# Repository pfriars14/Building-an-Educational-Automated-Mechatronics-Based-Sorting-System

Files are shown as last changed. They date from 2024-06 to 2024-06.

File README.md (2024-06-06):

The project integrates mechanical and electrical design, incorporating a robot arm, a microcontroller, sensors, and actuators. The sorting machine uses color identification to sort wooden blocks of three different colors. The blocks are stacked and dropped onto a conveyor belt by a hopper system that employs a solenoid actuator and a servo to release one block at a time at specific intervals. As the belt runs continuously, each block passes under a color sensor, which monitors the color and signals one of three servo-powered mechanical arms to guide the block into the appropriate chute. Each chute is equipped with a capacitive proximity sensor that sends a voltage signal to the robot controller, queuing commands for the robot to pick up the blocks from the bottom of each chute and return them to the hopper to form a continuously running sorting system. The project exemplifies a low-cost system that can be used in mechatronics education to illustrate the many challenges encountered in developing automated sorting systems.

This github site details project CAD files, videos, Arduino code, and a bill of materials.

NOTE: For the CAD section, "Ben Updated Design" is the final assembly, the rest of the files are parts which just need to be in the path in order to load. There is also another folder which just as a .step and .sldprt file for viewing the assembly surface geomtry.

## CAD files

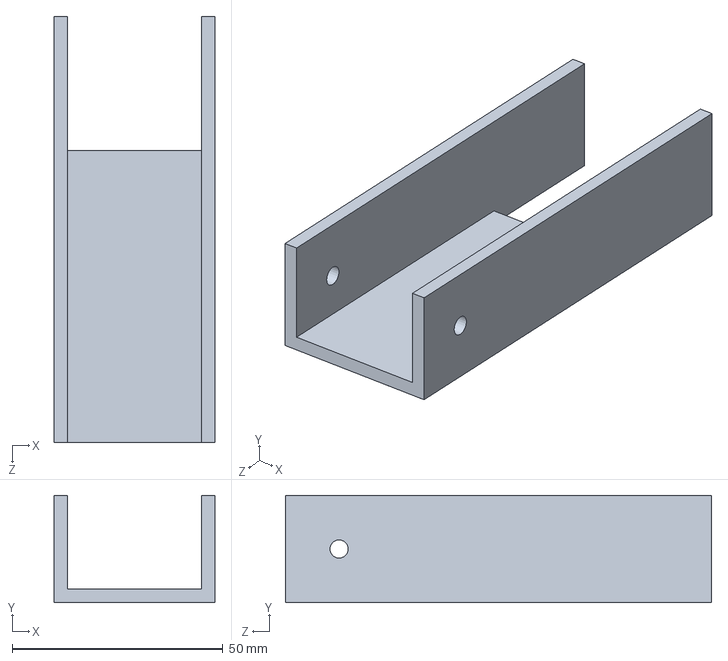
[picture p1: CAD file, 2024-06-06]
CAD Models/Wide Channel for Dropper.SLDPRT
38.1 x 25.4 x 101.0 mm

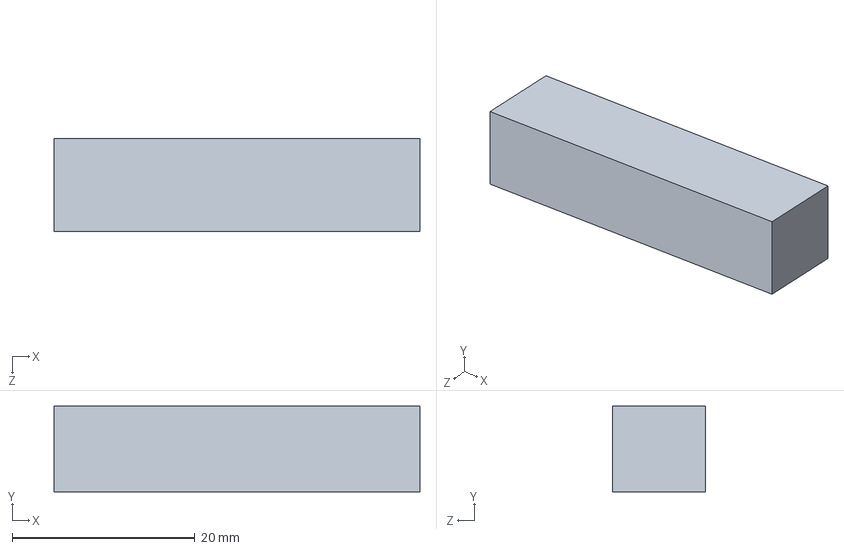
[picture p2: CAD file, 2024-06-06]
CAD Models/Body2.SLDPRT
40.0 x 9.36 x 10.2 mm

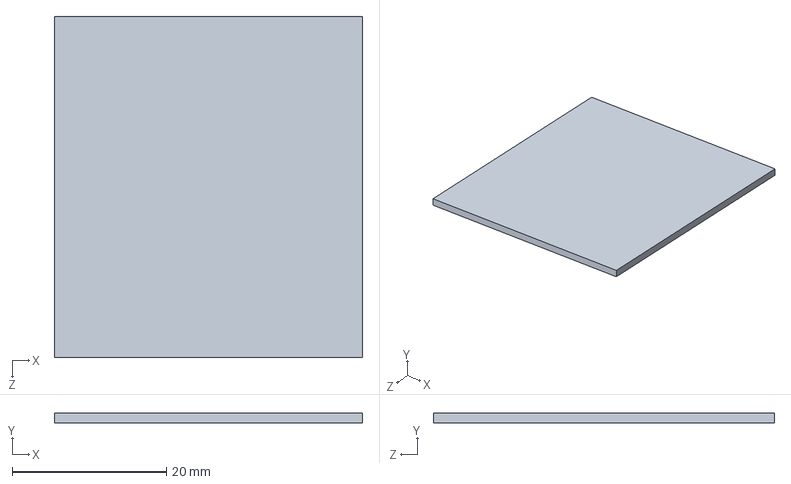
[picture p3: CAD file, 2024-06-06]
CAD Models/Body1.SLDPRT
40.0 x 1.27 x 44.3 mm

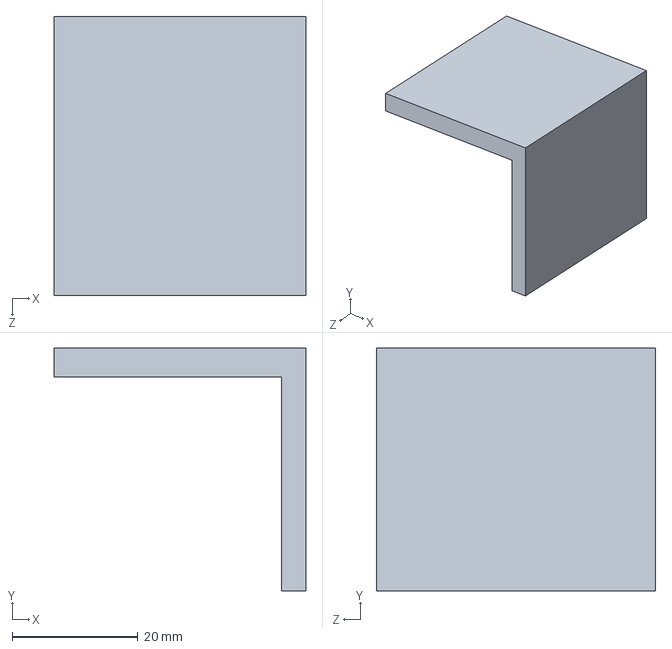
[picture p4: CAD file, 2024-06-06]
CAD Models/Body4.SLDPRT
40.0 x 38.6 x 44.3 mm

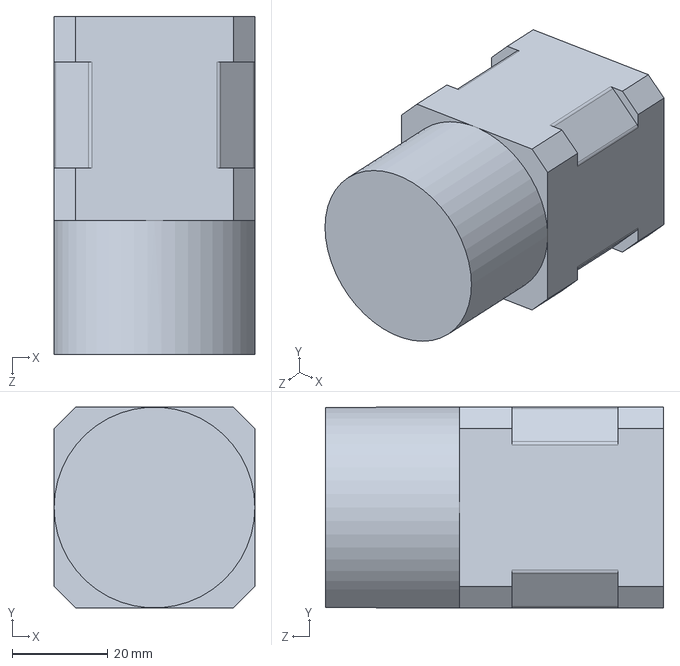
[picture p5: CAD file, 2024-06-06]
CAD Models/Stepper Motor.SLDPRT
42.0 x 42.0 x 70.7 mm

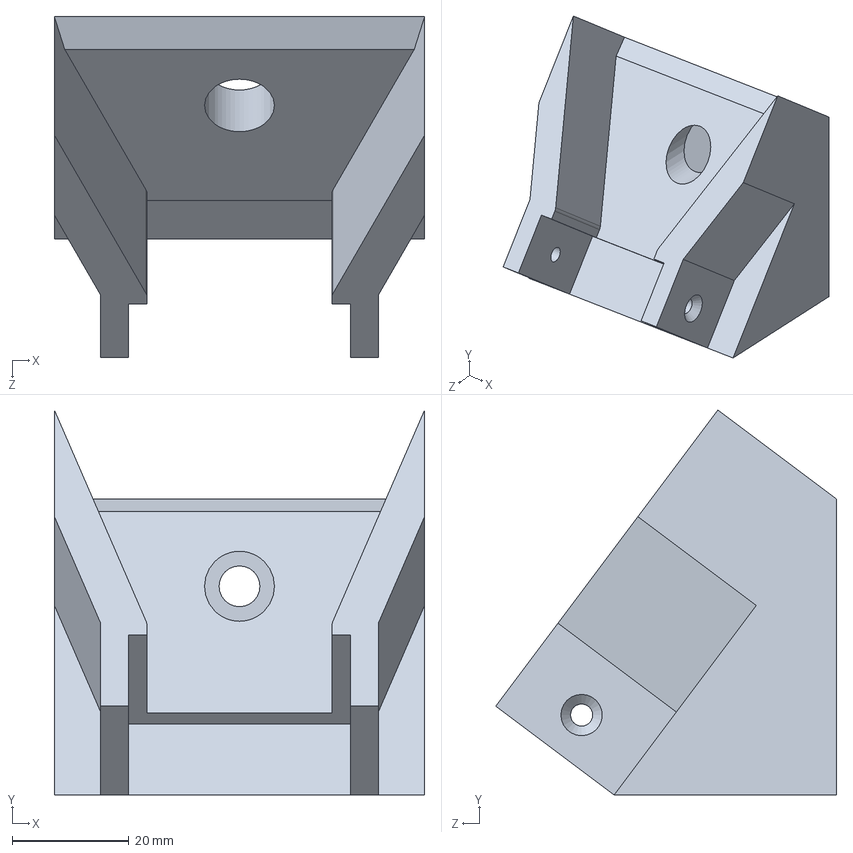
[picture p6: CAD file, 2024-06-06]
CAD Models/Ramp Attachment.SLDPRT
63.5 x 66.0 x 58.4 mm

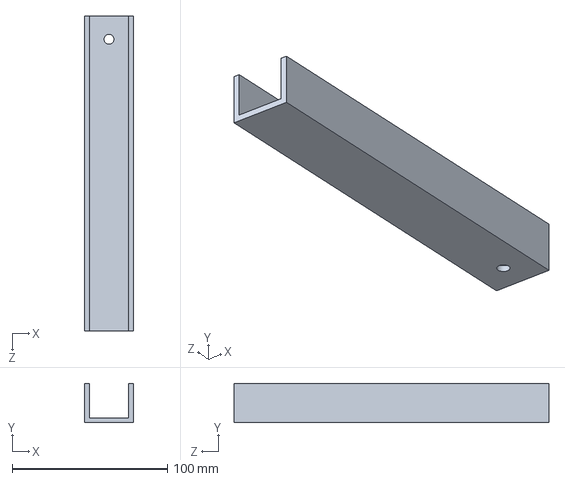
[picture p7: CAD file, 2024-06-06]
CAD Models/Conveyor Leg.SLDPRT
31.8 x 25.4 x 203.2 mm

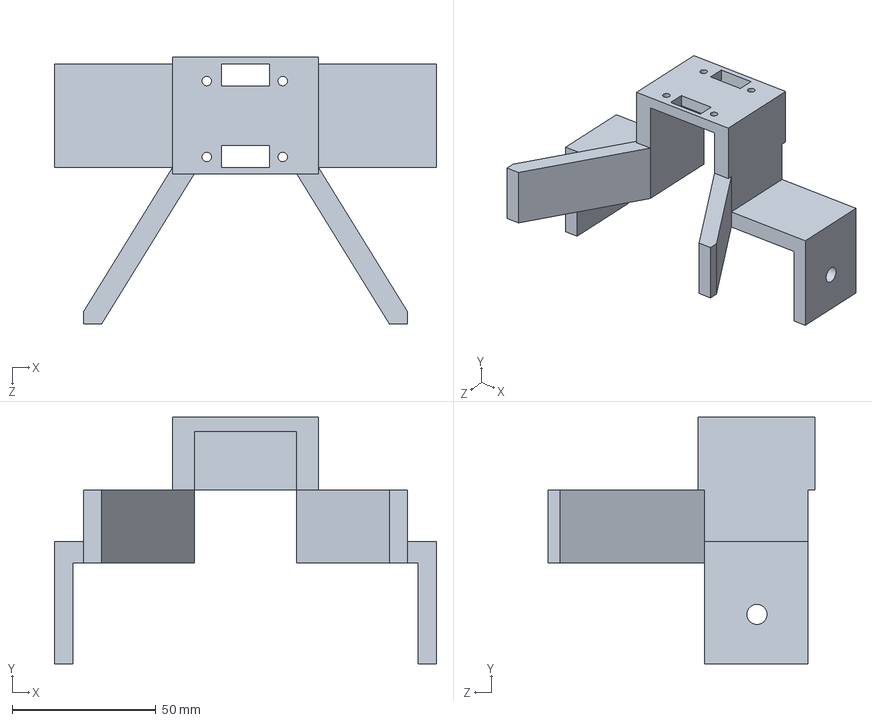
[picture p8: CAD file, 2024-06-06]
CAD Models/Funnel-Sensor Mount.SLDPRT
132.7 x 85.8 x 92.8 mm

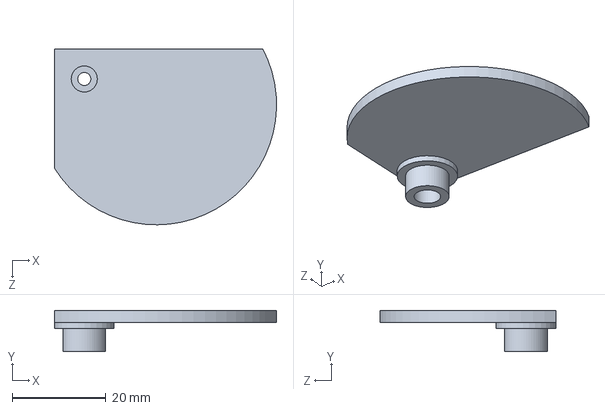
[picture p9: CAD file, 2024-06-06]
CAD Models/servo hopper.SLDPRT
47.3 x 8.79 x 37.4 mm

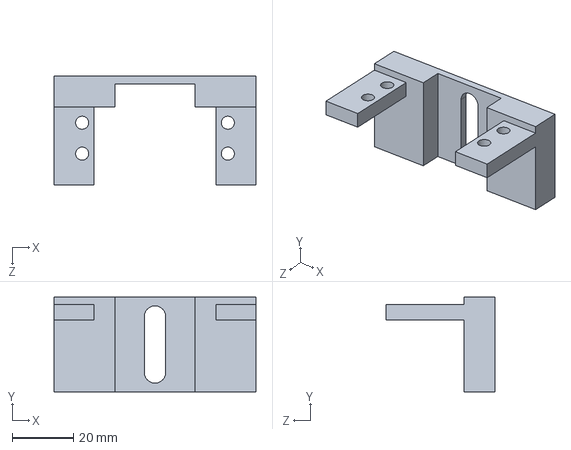
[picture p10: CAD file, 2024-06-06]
CAD Models/Servo Mount 1.SLDPRT
66.0 x 30.9 x 35.6 mm

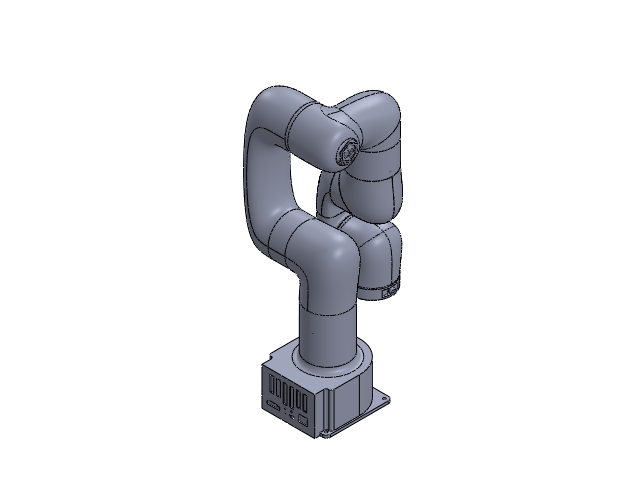
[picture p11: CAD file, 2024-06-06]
CAD Models/Lite 6(LI10XX).SLDASM
JOINT_III_1.STEP
HEADTOOL_1.STEP
JOINT_VI_1_1.STEP
JOINT_II_1.STEP
JOINT_IV_1_1.STEP
LOGO_RUBBER_CAP_1__1_1.STEP
JOINT_I_1_1.STEP
JOINT_V_1_1_ASM.STEP

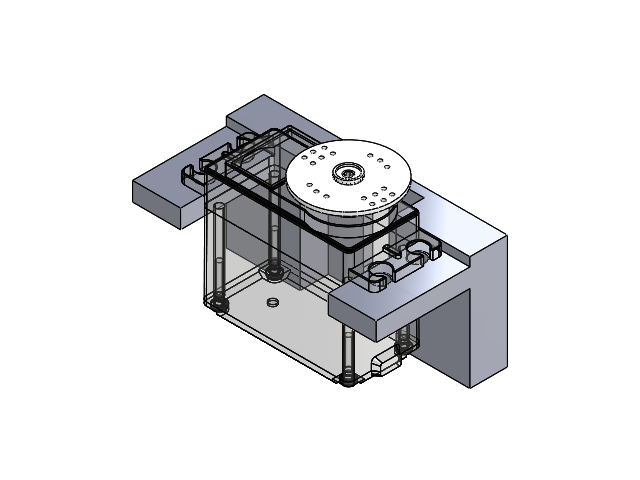
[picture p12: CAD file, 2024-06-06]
CAD Models/Servo Assembly.SLDASM
Servo Mount 1
_HS-311.stp
Spline

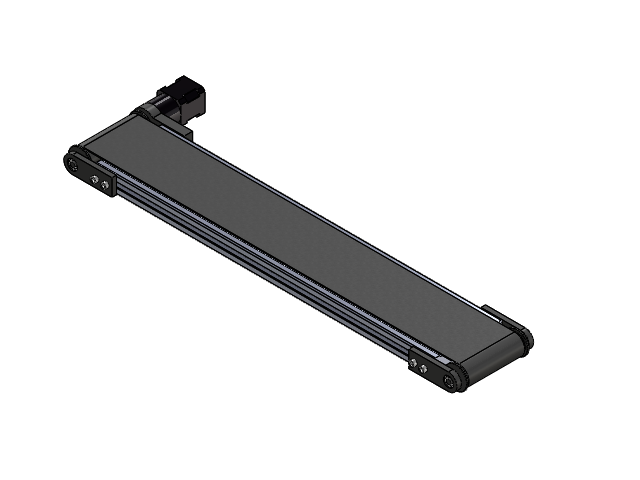
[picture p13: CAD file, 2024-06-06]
CAD Models/Conveyor Assembly.SLDASM
Belt Frame
Belt
Roller x 2
Side Bracket x 3
6656K76_Ultra-Thin Ball Bearing x 3
Stepper Bracket
Stepper Motor
96144A120_Fine-Thread Alloy Steel Socket Head Screw x 9

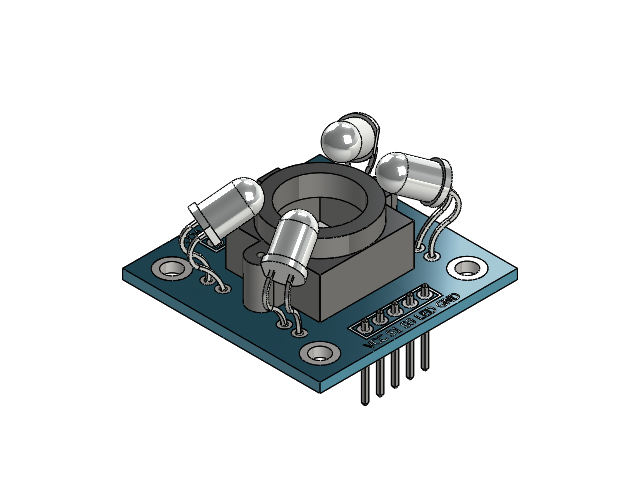
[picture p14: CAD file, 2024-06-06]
CAD Models/Color_sensor.SLDASM
Color_sensor_PCB.stp
Pin Header 1x5 TH Pitch 2.54mm.stp x 2
TCS3200.stp
5mm LED.stp
5mm LED_MIR.stp
5mm LED_MIR1.stp
5mm LED_MIR_MIR.stp
Screw GB_T 13806.2 A ST1.5 x 4.stp x 2

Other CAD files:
CAD Models/HS-311-1642818408.SLDASM
CAD Models/Sensor Assembly.SLDASM
CAD Models/Body3.SLDPRT
CAD Models/Clear tubing fix.SLDPRT
CAD Models/0837 solenoid.SLDPRT
CAD Models/6546K941_Multipurpose 6061 Aluminum Rectangular Tube.SLDPRT
CAD Models/6656K76_Ultra-Thin Ball Bearing.SLDPRT
CAD Models/7675K211_Universal-Object Proximity Switch (1).SLDPRT
CAD Models/8516K11_Clear Scratch and UV-Resistant Acrylic Rectangular Tube.SLDPRT
CAD Models/90044A280_Black-Oxide Alloy Steel Socket Head Screw.SLDPRT
CAD Models/90044A281_Black-Oxide Alloy Steel Socket Head Screw.SLDPRT
CAD Models/90275A145_Steel Slotted Flat Head Screws.SLDPRT
CAD Models/91290A326_Alloy Steel Socket Head Screw.SLDPRT
CAD Models/91864A085_Black-Oxide Alloy Steel Socket Head Screw.SLDPRT
CAD Models/96144A120_Fine-Thread Alloy Steel Socket Head Screw.SLDPRT
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

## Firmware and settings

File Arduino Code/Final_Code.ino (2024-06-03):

#include <Servo.h>

// Variables, definitions, etc..
unsigned long GetTimeNowMilli(void);
unsigned long GetTimeNowMicro(void);



// HopperTask
void HopperTask(void);
#define HopperActuatorPin 13
byte HopperState;
byte HopperNextState;
byte HopperState1Entry;
byte HopperState2Entry;
byte HopperState3Entry;
byte HopperState4Entry;
Servo servo4;
unsigned long HopperStartTime1 = 0;
unsigned long HopperStartTime2 = 0;
unsigned long HopperStartTime3 = 0;
unsigned long HopperStartTime4 = 0;



//Servo Task
void ServoTask(void);
byte ServoState;
byte ServoNextState;
byte ServoState1Entry;
byte ServoState2Entry;
byte ServoState3Entry;
byte ServoState4Entry;
unsigned long ServoStartTime1 = 0;
unsigned long ServoStartTime2 = 0;
unsigned long ServoStartTime3 = 0;
// int angle = 0;
Servo servo1;
Servo servo2;
Servo servo3;


// Stepper Task
void StepperMotorTask(void);
byte StepperState;
byte StepperNextState;
byte StepperState1Entry;
byte StepperState2Entry;
unsigned long StepperStartTime1 = 0;
unsigned long StepperStartTime2 = 0;
int StepPulse = 3;
int StepDir = 2;


//Color Sensor Task
void ColorSensorTask();
byte ColorState;
byte ColorNextState;
byte ColorState1Entry;
byte ColorState2Entry;
byte ColorState3Entry;
unsigned long ColorStartTime1 = 0;
unsigned long ColorStartTime2 = 0;
unsigned long ColorStartTime3 = 0;
int frequency = 0;
int color = 0;
int Rf = 0;
int Gf = 0;
int Bf = 0;
#define S0 4
#define S1 5
#define S2 6
#define S3 7
#define sensorOut 12


void setup() {

  // Misc.
  Serial.begin(9600);

  // Hopper Task
  pinMode(HopperActuatorPin, OUTPUT);
  HopperState1Entry = false;
  HopperState2Entry = false;
  HopperState3Entry = false;
  HopperState4Entry = false;
  servo4.attach(8);

  // Servo Task
  ServoState1Entry = false;
  ServoState2Entry = false;
  ServoState3Entry = false;
  ServoState4Entry = false;
  servo1.attach(9);
  servo2.attach(10);
  servo3.attach(11);


  //Color Sensor Task
  pinMode(S0, OUTPUT);
  pinMode(S1, OUTPUT);
  pinMode(S2, OUTPUT);
  pinMode(S3, OUTPUT);
  pinMode(sensorOut, INPUT);
  digitalWrite(S0, HIGH);
  digitalWrite(S1, HIGH);
  ColorState1Entry = false;
  ColorState2Entry = false;
  ColorState3Entry = false;


  // Stepper Task
  pinMode(StepPulse, OUTPUT);
  pinMode(StepDir, OUTPUT);
  digitalWrite(StepDir, LOW);
  StepperState1Entry = false;
  StepperState2Entry = false;
}





void loop() {

  StepperNextState = 1;
  ColorNextState = 1;
  ServoNextState = 1;
  HopperNextState = 1;

  while (2 > 1) {
    HopperTask();
    ServoTask();
    StepperMotorTask();
    ColorSensorTask();
    // Serial.println(color);
  }
}





void HopperTask(void) {
  HopperState = HopperNextState;

  switch (HopperState) {

    case 1:

      if (HopperState1Entry == false) {
        servo4.write(300);
        digitalWrite(HopperActuatorPin, LOW);
        HopperStartTime1 = GetTimeNowMilli();
        HopperState1Entry = true;
      }
      if (GetTimeNowMilli() - HopperStartTime1 >= 5000){
        HopperState1Entry = false;
        HopperNextState = 2;
      }
      break;


    case 2:

      if (HopperState2Entry == false) {
        // servo4.write(300);
        digitalWrite(HopperActuatorPin, HIGH);
        HopperStartTime2 = GetTimeNowMilli();
        HopperState2Entry = true;
      }
      if (GetTimeNowMilli() - HopperStartTime2 >= 300){
        HopperState2Entry = false;
        HopperNextState = 3;
      }
      break;


    case 3:

      if (HopperState3Entry == false) {
        servo4.write(0);
        // digitalWrite(HopperActuatorPin, HIGH);
        HopperStartTime3 = GetTimeNowMilli();
        HopperState3Entry = true;
      }
      if (GetTimeNowMilli() - HopperStartTime3 >= 2000){
        HopperState3Entry = false;
        HopperNextState = 4;
      }
      break;


    case 4:

      if (HopperState4Entry == false) {
        servo4.write(300);
        // digitalWrite(HopperActuatorPin, HIGH);
        HopperStartTime4 = GetTimeNowMilli();
        HopperState4Entry = true;
      }
      if (GetTimeNowMilli() - HopperStartTime4 >= 750){
        HopperState4Entry = false;
        HopperNextState = 1;
      }
      break;
  }
}




void ServoTask(void) {
  ServoState = ServoNextState;
  switch (ServoState) {
    case 1:

      if (ServoState1Entry == false) {
        servo1.write(0);
        servo2.write(0);
        servo3.write(0);
        ServoState1Entry = true;
      }
      if (color == 1) {
        ServoNextState = 2;
        ServoState1Entry = false;
      }
      if (color == 2) {
        ServoNextState = 3;
        ServoState1Entry = false;
      }
      if (color == 3) {
        ServoNextState = 4;
        ServoState1Entry = false;
      }
      break;

    case 2:
      if (ServoState2Entry == false) {
        servo1.write(45);
        servo2.write(0);
        servo3.write(0);
        ServoStartTime1 = GetTimeNowMilli();
        ServoState2Entry = true;
      }
      if (GetTimeNowMilli() - ServoStartTime1 >= 5000) {
        ServoState2Entry = false;
        ServoNextState = 1;
        color = 0;
      }
      break;

    case 3:
      if (ServoState3Entry == false) {
        servo1.write(0);
        servo2.write(52);
        servo3.write(0);
        ServoStartTime2 = GetTimeNowMilli();
        ServoState3Entry = true;
      }
      if (GetTimeNowMilli() - ServoStartTime2 >= 5000) {
        ServoState3Entry = false;
        ServoNextState = 1;
        color = 0;
      }
      break;

    case 4:
      if (ServoState4Entry == false) {
        servo1.write(0);
        servo2.write(0);
        servo3.write(47);
        ServoStartTime3 = GetTimeNowMilli();
        ServoState4Entry = true;
      }
      if (GetTimeNowMilli() - ServoStartTime3 >= 5000) {
        ServoState4Entry = false;
        ServoNextState = 1;
        color = 0;
      }
      break;
  }
}







void StepperMotorTask(void) {

  StepperState = StepperNextState;

  // Serial.println(StepperState);

  switch (StepperState) {
    case 1:

      if (StepperState1Entry == false) {
        digitalWrite(StepPulse, HIGH);
        StepperStartTime1 = GetTimeNowMicro();
        StepperState1Entry = true;
      }
      if (GetTimeNowMicro() - StepperStartTime1 >= 407) {
        StepperState1Entry = false;
        StepperNextState = 2;
      }

      break;

    case 2:
      if (StepperState2Entry == false) {
        digitalWrite(StepPulse, LOW);
        StepperStartTime2 = GetTimeNowMicro();
        StepperState2Entry = true;
      }
      if (GetTimeNowMicro() - StepperStartTime2 >= 407) {
        StepperState2Entry = false;
        StepperNextState = 1;
      }
      break;
  }
}




void ColorSensorTask(void) {
  ColorState = ColorNextState;



  switch (ColorState) {
    case 1:

      if (ColorState1Entry == false) {
        digitalWrite(S2, LOW);
        digitalWrite(S3, LOW);
        Rf = pulseIn(sensorOut, LOW);
        ColorStartTime1 = GetTimeNowMilli();
        ColorState1Entry = true;
      }
      if (GetTimeNowMilli() - ColorStartTime1 >= 10) {
        ColorState1Entry = false;
        ColorNextState = 2;
      }

      break;

    case 2:
      if (ColorState2Entry == false) {
        digitalWrite(S2, HIGH);
        digitalWrite(S3, HIGH);
        Gf = pulseIn(sensorOut, LOW);

        ColorStartTime2 = GetTimeNowMilli();
        ColorState2Entry = true;
      }
      if (GetTimeNowMilli() - ColorStartTime2 >= 10) {
        ColorState2Entry = false;
        ColorNextState = 3;
      }
      break;

    case 3:
      if (ColorState3Entry == false) {
        digitalWrite(S2, LOW);
        digitalWrite(S3, HIGH);
        // Reading the output frequency
        Bf = pulseIn(sensorOut, LOW);

        if (Rf<25 & Rf>15 & Gf<40 & Gf>33 & Bf<40 & Bf>30) {
          color = 2; //Red
        }
        if (Rf<60 & Rf>40 & Gf<40 & Gf>20 & Bf<30 & Bf>10) {
          color = 1; //Blue
        }
        if (Rf<30 & Rf>20 & Gf<23 & Gf>10 & Bf<30 & Bf>20) {
          color = 3; //Green
        }
        if (Rf < 53 && Rf > 44 && Gf < 51 && Gf > 47 && Bf < 48 && Bf > 43) {
          color = 0;
        }
        ColorStartTime3 = GetTimeNowMilli();
        ColorState3Entry = true;
      }
      if (GetTimeNowMilli() - ColorStartTime3 >= 10) {
        ColorState3Entry = false;
        ColorNextState = 1;
      }
      break;
  }
}



// Timers

unsigned long GetTimeNowMilli(void) {
  return (millis());
}


unsigned long GetTimeNowMicro(void) {
  return (micros());
}
